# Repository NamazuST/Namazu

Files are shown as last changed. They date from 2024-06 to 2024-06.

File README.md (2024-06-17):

# Namazu: Low-cost tunable shaking table for vibration experiments under generic signals

This repository contains supplementary material to the publication ["2024 Grashorn, Bittner, Banse et al. - Namazu: Low-cost tunable shaking table for vibration experiments under generic signals"](https://doi.org/10.1007/s40799-024-00727-8) published in Experimental Techniques. The repository contains software, coded examples, firmware, and CAD files usable for vibrational experiments in the context of dynamic analysis of structures and stochastic dynamics in general.

Updates 17.06.2024

# Namazu architecture (Software & Hardware)

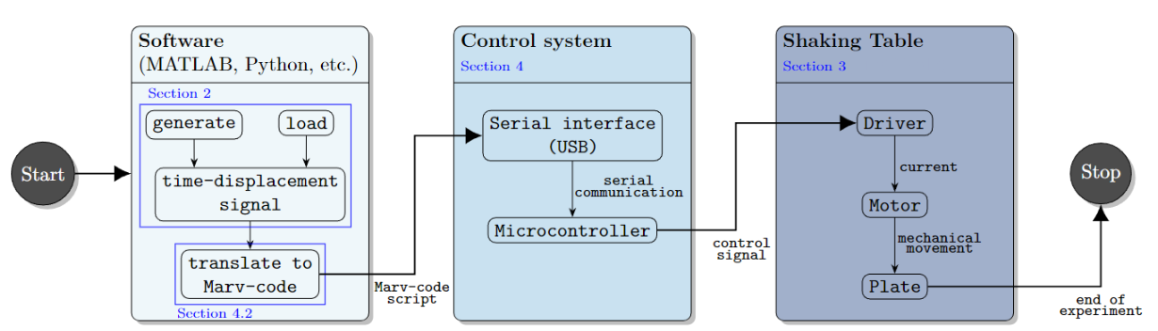
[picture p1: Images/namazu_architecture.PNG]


Figure 1: Flowchart and design concept of the Namazu framework, from signal generation via the software over the control system to plate motion, as in [our paper.](https://doi.org/10.1007/s40799-024-00727-8)

# Preparations

When this readme was written the following OS, platforms, and software were used:

- Windows 10.0.19041.4355 (professional)
- Microsoft Visual Studio Code 1.90.0 (VSC)
- MATLAB version 2023a
- Python version 3.12.3
- PlatformIO with Core 6.1.15 and Home 3.4.4

It is necessary to upload the firmware to a compatible ESP32 device. If this readme is not enough, you can find more information here: ["Namazu documentation"](https://namazu.de/). Please note that there are a multitude of ESP32 variants, so far we tested NodeMCU ESP32 WROOM32 and Firebeetle ESP32 modules. Please also note that we cannot test every variant and we are currently not recommending using ESP32-S2 or -C3 variants, since this could require code adaptations.

# Flashing of ESP32

Connect the ESP32 via a USB cable with your computer and identify the USB port by e.g. the device manager or PlatformIO.

In Windows you should located something like this:
"Port: COM3; Description: Silicon Labs CP210x USB to UART Bridge (COM3); Hardware: USB VID:PID=10C4:EA60 SER=0001 LOCATION=1-6"
The port ``` COM3 ``` could have a different number on your machine, depending on the USB socket you used.
In Linux the port is displayed differently (e.g. ```/dev/ttyUSB0```), but the description should remain the same.

Start VSC, locate and navigate to the Firmware folder (``\Firmware\``), start PlatformIO (in VSC), make sure the ESP32 has been located as described above.
To verify that everything is installed okay and no libraries are missing, press build. As indicated by <span style="color:orange"> *1.* </span> in Figure 2 below. Alternatively you can also use the buttons that are normally in the VSC UI located in the top-right corner, here see <span style="color:yellow"> *4.* </span> Figure 2.

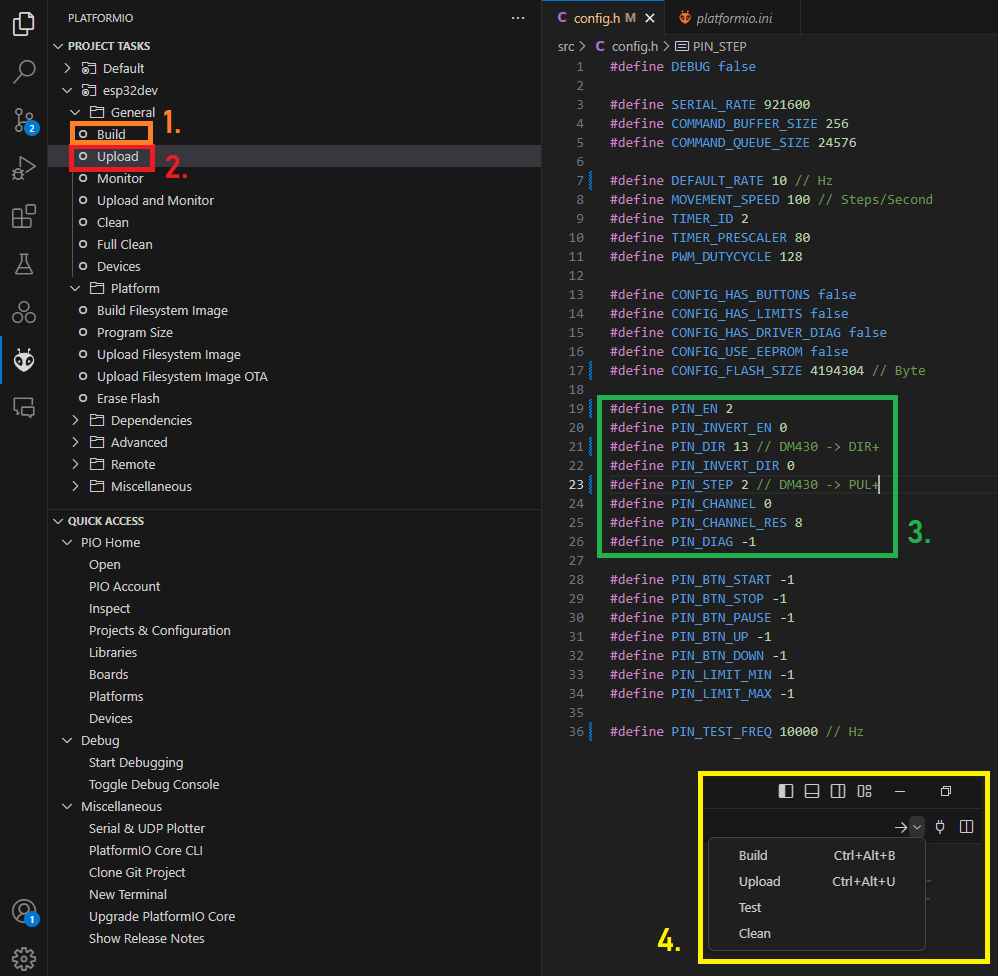
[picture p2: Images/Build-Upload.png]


Figure 2: PlatformIO.

A successful build should reveal this:



Figure 3: Build.

Then upload by pressing the upload button (inicated by <span style="color:red"> *2.* </span> in Figure 2 above) in PlatformIO. VSC will build again and then upload, the COM port should be identified automatically. 

A successful upload should display this:

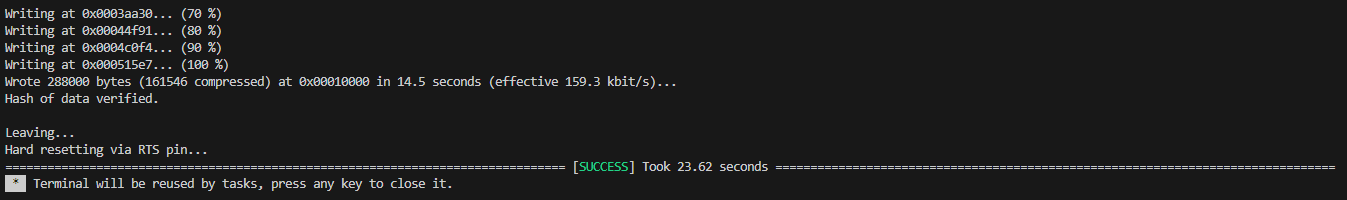
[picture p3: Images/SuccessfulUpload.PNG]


Figure 4: Upload.

The connecting pins of your ESP32 to the driver (in our case we used a DM430) are given in the window as in <span style="color:green"> *3.* </span> in Figure 2.

We advise you to not change or touch the firmware software in ``\Firmware\``, unless you know what you are doing.

## Safety Precautions

Remember, if you built Namazu, you are dealing with machinery.

<span style="color:red">*Disclaimer*</span>: The authors assume no responsibility or liability for any use of the software and provided ideas. By using this software, you acknowledge that you are solely responsible for any consequences that may arise. It is your responsibility to ensure you fully understand the operation and potential risks associated with the software and any machinery or systems it controls.

<span style="color:red">*Safety Warning*</span>: Always ensure you have a reliable power switch or safety mechanism to completely disconnect the machinery from the power grid in case of an emergency. Thoroughly assess the risks and plan your actions carefully. Double-check all connections and settings before proceeding. Safety should always be your top priority.

# Start with a main file

We provided coded examples and implementations for MATLAB and Python. Once you have your hardware ready and safety precautions were taken, we suggest to start with simple examples.

## MATLAB

For MATLAB, go to ```\MATLAB\MainCreateSimulation.m```. Here check line 179.

Make sure the correct com port is stated. If ran successfully a fixed harmonic with amplitude 1 and frequency 1 is started.

```Matlab
%% find shaking table controller on the correct COM port, COM port needs to be identified manually

dev = serialport("COM3",921600);
```

## Python

For Python, go to ```\Python\main_FixedHarmonic.py```. There check line 47.

Make sure the correct com port is stated. If ran successfully a fixed harmonic with amplitude 1 and frequency 1 is started.

```py
# Set the COM port and baud rate according to your ESP32 configuration
com_port = 'COM3'  # Change this to your COM port on Windows, e.g., 'COM3'
baud_rate = 921600  # Change this to match your ESP32 configuration

# Open the serial connection
ser = serial.Serial(com_port, baud_rate, timeout=1)
```

## Cite

For technical paper:

Grashorn J., Bittner, M., Banse, M. et al. (2024). Namazu: Low-cost tunable shaking table for vibration experiments under generic signals [https://doi.org/10.1007/s40799-024-00727-8](https://doi.org/10.1007/s40799-024-00727-8)

BibTex:
```
@article{NamazuEXTE2024,
    author = {Grashorn J., Bittner, M., Banse, M., Chang, X., Beer, M., Fau, A.},
    title = {Namazu: Low-cost tunable shaking table for vibration experiments under generic signals},
    year = {2024},
    publisher = {Springer Nature},
    journal = {Experimental Techniques},
    doi = {10.1007/s40799-024-00727-8},
}
```

For the repository:

https://github.com/NamazuST/Namazu

doi: https://zenodo.org/doi/10.5281/zenodo.10533795

BibTex:
```
@misc{NamazuRepo2024,
    author = {Grashorn J., Bittner, M., Banse, M.},
    title = {Namazu},
    year = {2024},
    publisher = {GitHub},
    journal = {GitHub repository},
    doi = {10.5281/zenodo.10533795},
}
```

## Showcase

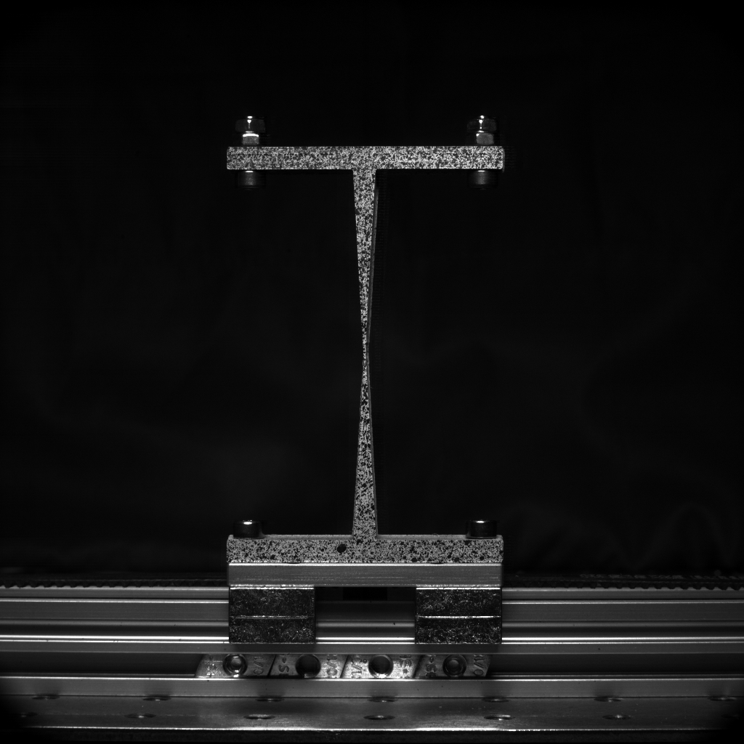
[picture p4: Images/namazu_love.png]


Figure 5: Experimental campaign with a Namazu realization, a 3D printed specimen and love

## Disclaimer
1. Content.
The author reserves the right not to be responsible for the topicality, correctness, completeness or quality of the information provided. Liability claims regarding damage caused by the use of any information provided, including any kind of information which is incomplete or incorrect, will therefore be rejected.
All offers are not-binding and without obligation. Parts of the pages or the complete publication including all offers and information might be extended, changed or partly or completely deleted by the author without separate announcement.
2. Responsibility. The authors assume no responsibility or liability for any use of the software and provided ideas. By using this software, you acknowledge that you are solely responsible for any consequences that may arise. It is your responsibility to ensure you fully understand the operation and potential risks associated with the software and any machinery or systems it controls.
3. Referrals and links.
The author is not responsible for any contents linked or referred to from his pages - unless he has full knowledge of illegal contents and would be able to prevent the visitors of his site fromviewing those pages. If any damage occurs by the use of information presented there, only the author of the respective pages might be liable, not the one who has linked to these pages. Furthermore the author is not liable for any postings or messages published by users of discussion boards, guestbooks or mailinglists provided on his page.
4. Copyright.
The author aims to use only non-copyrighted material or materials for which the author has obtained the necessary permissions. In cases where this is not possible, the copyright of the respective material will be indicated. The copyright for any original material created by the author is reserved. Duplication or use of such materials, including but not limited to images, diagrams, sounds, or texts, in other electronic or printed publications is permitted only under the terms of the included licenses:
    - Repository: Licensed under the Creative Commons Attribution-NonCommercial-ShareAlike 4.0 International (["CC BY-NC-SA 4.0"](https://creativecommons.org/licenses/by-nc-sa/4.0/)) license.
    - Technical Paper: Licensed under the Creative Commons Attribution 4.0 International (["CC BY 4.0"](https://creativecommons.org/licenses/by/4.0/)) license.
5. Privacy policy.
No privacy data is collected.
6. Legal validity of this disclaimer.
This disclaimer is to be regarded as part of the internet publication which you were referred from. If sections or individual terms of this statement are not legal or correct, the content or validity of the other parts remain uninfluenced by this fact.

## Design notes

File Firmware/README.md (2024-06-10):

# shakeIt

Available commands:

- **start** - Starts to move the motor to previously specified positions
- **stop** - immediately stops motor movement
- **info** - responds a line of information according the machines state:
`OK: Info: state: READY, mode POSITION, command 25 of 25, rate: 20hz, spmm: 10`

- **set rate nnn.nnn** - set the amout of positions to handle in one second
- **set spmm** - specifies how many steps the motor has to drive to move the carriage one millimeter
- **set mode position/velocity** - changes the interpretation of specified data
- **add nnn.nnn** - adds a position at the end of list
- **reset** - removes all positions from memory

This is an exemplary program to transmit via serial:
```
reset
set spmm 10
set rate 2.5
set mode pos
add 1
add 16
add 20
add 21
add 18
add 0.5
add -20
add -22
add -20
add -10
add 0
start
```

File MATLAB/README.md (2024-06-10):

# Shaking Table

## WARNING

!!!THE CONTROLLER SOFTWARE CURRENTLY HAS _NO_ SAFETY FEATURES (SUCH AS LIMIT SWITCHES), BE CAREFUL WHEN USING METHODS THAT WERE NOT TESTED EXTENSIVELY. INJURY TO YOU OR THE TABLE IS POSSIBLE!!!
It is entirely possible that settings in the simulation code and in the controller contradict each other. E.g. if the motor has a different value for the time step size, the table might behave very unexpectedly.

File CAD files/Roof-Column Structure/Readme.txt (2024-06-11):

Requirements: OpenSCAD

Scripts and OpenSCAD files to generate a 3D-printable roof-column structure for dynamical experiments. The structure is fully parameterized, where the spring stiffnesses can be changed based on thickness, number of windings etc. The roof can either be made with two or four springs.
A script (for Linux) is provided to export stl files for 3D-printing for the springs and the plate. An stl for the full assembly based on number of springs and number of storeys is also generated.
Attachement holes for MPU6050 sensors are included.

Usage:

- Change parameters to desired layout in scripts/Modules.scad, press F5 in OpenSCAD to view the model
- Run compile.sh from command line (Linux) to generate stl-files

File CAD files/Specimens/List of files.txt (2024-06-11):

- ContactColumn.stl
	Column with thin middle layer and contact area
	
- NotchedBeam.stl
	Beam with notch to induce damage

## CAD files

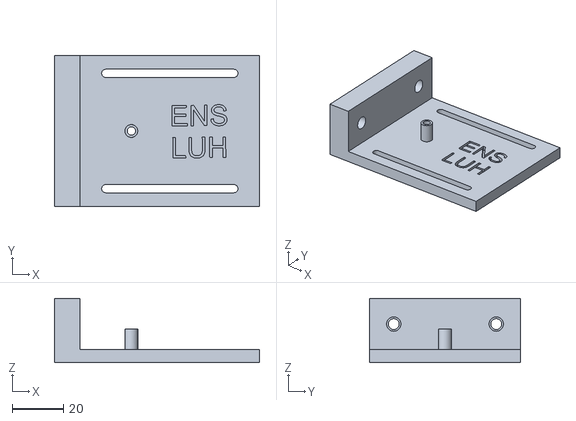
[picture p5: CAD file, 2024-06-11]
CAD files/Assembly/Belt tensioner/BeltTensioner_2.stl
80.0 x 58.8 x 25.0

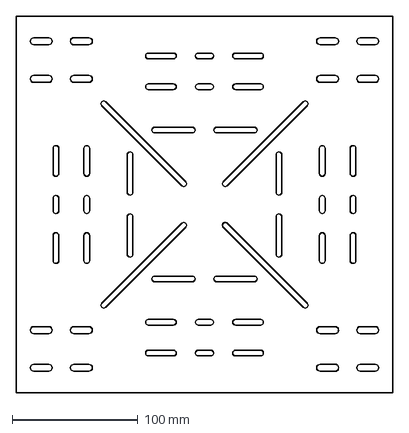
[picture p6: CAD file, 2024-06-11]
CAD files/Assembly/Plate/Plate.dxf
300.0 x 300.0 mm

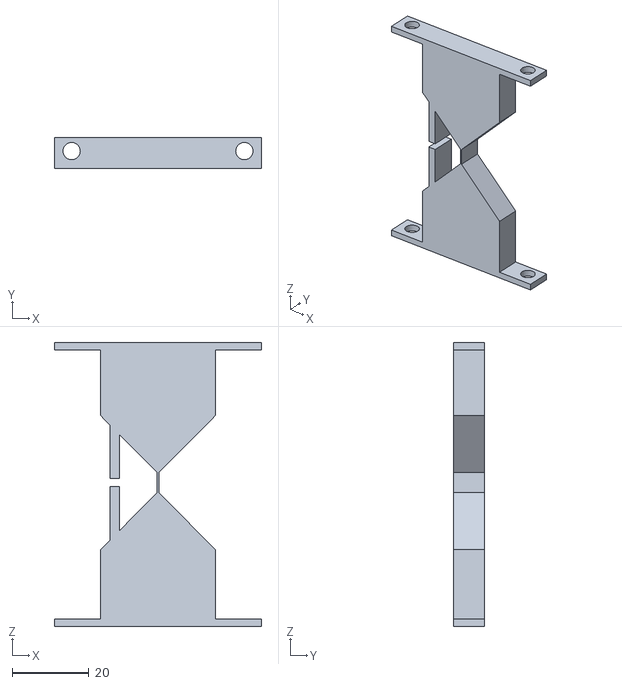
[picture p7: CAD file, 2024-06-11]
CAD files/Specimens/ContactColumn.stl
54.0 x 8.00 x 74.0

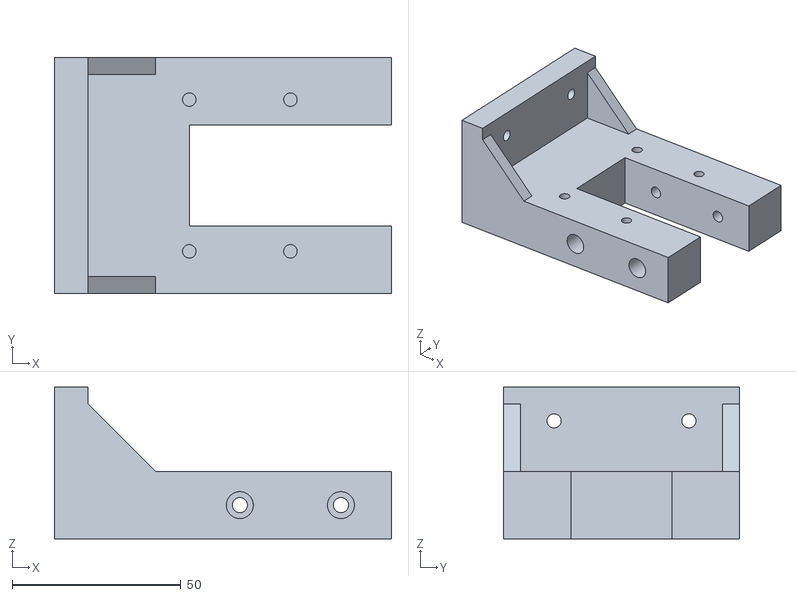
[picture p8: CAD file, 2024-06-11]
CAD files/Assembly/Belt tensioner/BeltTensioner_1.stl
100.0 x 70.0 x 45.0

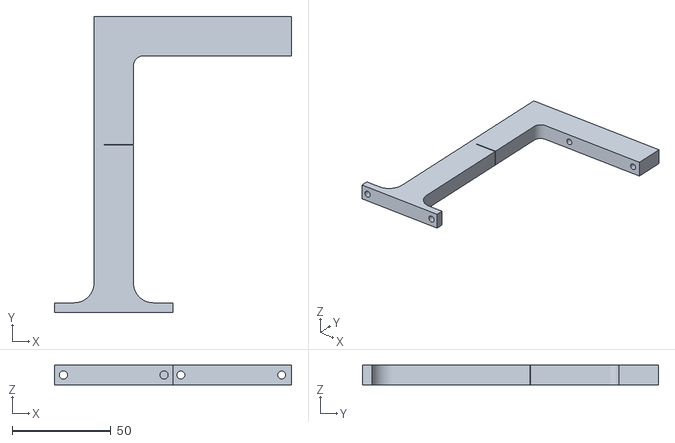
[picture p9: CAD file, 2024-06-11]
CAD files/Specimens/NotchedBeam.stl
120.0 x 150.0 x 10.0

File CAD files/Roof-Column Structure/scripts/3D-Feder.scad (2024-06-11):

include <Modules.scad>

Feder();

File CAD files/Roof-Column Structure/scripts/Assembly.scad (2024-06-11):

include <Modules.scad>

MPUattachments = 0;
dHole = 0;
nutS = 0;

module Assembly() {
        translate([0,0,wBase/2])
        for (i=[0:nStoreys-1]) {
            translate([0,0,i*storeyHeight])
            Storey();
        }
}

Assembly();

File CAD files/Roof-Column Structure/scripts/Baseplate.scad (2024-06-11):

include <Modules.scad>

Plate();

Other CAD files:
CAD files/Roof-Column Structure/scripts/BaseplateCutout.scad
CAD files/Roof-Column Structure/scripts/Modules.scad
CAD files/Roof-Column Structure/scripts/spring.scad

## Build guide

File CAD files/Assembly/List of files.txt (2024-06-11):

- Plate/Plate.dxf
	attachment plate to attach specimens on top of the table
	
- Belt tensioner/
	3D printable assembly to attach and tension the belt on the opposite side of the motor

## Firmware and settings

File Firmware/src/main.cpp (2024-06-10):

#include <Arduino.h>
#include "config.h"

#include <si_machine.hpp>
#include <si_interface.hpp>
#include <si_storage.hpp>

si::Storage storage;
si::Machine machine = si::Machine(storage);
si::Interface interface = si::Interface(machine);

#if CONFIG_HAS_BUTTONS
/* START - Button */
IRAM_ATTR void btn_start();
void start(void *) {
    interface.cmd_start();
    attachInterrupt(PIN_BTN_START,btn_start,FALLING);
}
IRAM_ATTR void btn_start() {
    detachInterrupt(PIN_BTN_START);
    xTaskCreate(
        start,              /* Task function. */
        "BtnStart",         /* String with name of task. */
        4096,               /* Stack size in bytes. */
        NULL,               /* Parameter passed as input of the task */
        0,                  /* Priority of the task. */
        NULL
    );
}

/* STOP - Button */
IRAM_ATTR void btn_stop();
void stop(void *) {
    interface.cmd_stop();
    attachInterrupt(PIN_BTN_STOP,btn_stop,FALLING);
}
IRAM_ATTR void btn_stop() {
    detachInterrupt(PIN_BTN_STOP);
    xTaskCreate(
        stop,               /* Task function. */
        "BtnStop",          /* String with name of task. */
        4096,               /* Stack size in bytes. */
        NULL,               /* Parameter passed as input of the task */
        0,                  /* Priority of the task. */
        NULL
    );
}

/* PAUSE - Button */
IRAM_ATTR void btn_pause();
void pause(void *) {
    machine.pause();
    attachInterrupt(PIN_BTN_PAUSE,btn_pause,FALLING);
}
IRAM_ATTR void btn_pause() {
    detachInterrupt(PIN_BTN_PAUSE);
    xTaskCreate(
        pause,              /* Task function. */
        "BtnPause",         /* String with name of task. */
        4096,               /* Stack size in bytes. */
        NULL,               /* Parameter passed as input of the task */
        0,                  /* Priority of the task. */
        NULL
    );
}

/* UP - Button */
IRAM_ATTR void btn_up_rise();
void up_rise(void *) {
    machine.stop();
    attachInterrupt(PIN_BTN_UP,btn_up_rise,FALLING);
}
IRAM_ATTR void btn_up_rise() {
    detachInterrupt(PIN_BTN_UP);
    xTaskCreate(
        up_rise,            /* Task function. */
        "BtnUpRise",        /* String with name of task. */
        4096,               /* Stack size in bytes. */
        NULL,               /* Parameter passed as input of the task */
        0,                  /* Priority of the task. */
        NULL
    );
}
IRAM_ATTR void btn_up_fall();
void up_fall(void *) {
    machine.move_up();
    attachInterrupt(PIN_BTN_UP,btn_up_rise,RISING);
}
IRAM_ATTR void btn_up_fall() {
    detachInterrupt(PIN_BTN_UP);
    xTaskCreate(
        up_fall,            /* Task function. */
        "BtnUpFall",        /* String with name of task. */
        4096,               /* Stack size in bytes. */
        NULL,               /* Parameter passed as input of the task */
        0,                  /* Priority of the task. */
        NULL
    );
}

/* DOWN - Button */
IRAM_ATTR void btn_down_rise();
void down_rise(void *) {
    machine.stop();
    attachInterrupt(PIN_BTN_DOWN,btn_down_rise,FALLING);
}
IRAM_ATTR void btn_down_rise() {
    detachInterrupt(PIN_BTN_DOWN);
    xTaskCreate(
        down_rise,          /* Task function. */
        "BtnUpRise",        /* String with name of task. */
        4096,               /* Stack size in bytes. */
        NULL,               /* Parameter passed as input of the task */
        0,                  /* Priority of the task. */
        NULL
    );
}
IRAM_ATTR void btn_down_fall();
void down_fall(void *) {
    machine.move_down();
    attachInterrupt(PIN_BTN_DOWN,btn_down_rise,RISING);
}
IRAM_ATTR void btn_down_fall() {
    detachInterrupt(PIN_BTN_DOWN);
    xTaskCreate(
        down_fall,            /* Task function. */
        "BtnUpFall",        /* String with name of task. */
        4096,               /* Stack size in bytes. */
        NULL,               /* Parameter passed as input of the task */
        0,                  /* Priority of the task. */
        NULL
    );
}
#endif

#if CONFIG_HAS_LIMITS
/* Limit Switch MIN */
IRAM_ATTR void limit_min();
void min(void *) {
    machine.limit_min();
    attachInterrupt(PIN_LIMIT_MIN,limit_min,FALLING);
}
IRAM_ATTR void limit_min() {
    detachInterrupt(PIN_LIMIT_MIN);
    xTaskCreate(
        min,              /* Task function. */
        "LimitMin",         /* String with name of task. */
        4096,               /* Stack size in bytes. */
        NULL,               /* Parameter passed as input of the task */
        0,                  /* Priority of the task. */
        NULL
    );
}

/* Limit Switch MAX */
IRAM_ATTR void limit_max();
void max(void *) {
    machine.limit_max();
    attachInterrupt(PIN_LIMIT_MAX,limit_max,FALLING);
}
IRAM_ATTR void limit_max() {
    detachInterrupt(PIN_LIMIT_MAX);
    xTaskCreate(
        max,                /* Task function. */
        "LimitMax",         /* String with name of task. */
        4096,               /* Stack size in bytes. */
        NULL,               /* Parameter passed as input of the task */
        0,                  /* Priority of the task. */
        NULL
    );
}
#endif

/* MAIN */
void setup() {
    interface.init();
    machine.init();
    if (!storage.init()) {
        Serial.println("FAILED TO INITALIZE STORAGE");
    }
#if CONFIG_HAS_LIMITS
    attachInterrupt(PIN_LIMIT_MIN,limit_min,FALLING);
    attachInterrupt(PIN_LIMIT_MAX,limit_max,FALLING);
#endif
#if CONFIG_HAS_BUTTONS
    attachInterrupt(PIN_BTN_START,btn_start,FALLING);
    attachInterrupt(PIN_BTN_STOP,btn_stop,FALLING);
    attachInterrupt(PIN_BTN_PAUSE,btn_pause,FALLING);
    attachInterrupt(PIN_BTN_UP,btn_up_fall,FALLING);
    attachInterrupt(PIN_BTN_DOWN,btn_down_fall,FALLING);
#endif

}

void loop() {
    interface.loop();
}

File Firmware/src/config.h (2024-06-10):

#define DEBUG false

#define SERIAL_RATE 921600
#define COMMAND_BUFFER_SIZE 256
#define COMMAND_QUEUE_SIZE 24576

#define DEFAULT_RATE 10 // Hz
#define MOVEMENT_SPEED 100 // Steps/Second
#define TIMER_ID 2
#define TIMER_PRESCALER 80
#define PWM_DUTYCYCLE 128

#define CONFIG_HAS_BUTTONS false
#define CONFIG_HAS_LIMITS false
#define CONFIG_HAS_DRIVER_DIAG false
#define CONFIG_USE_EEPROM false
#define CONFIG_FLASH_SIZE 4194304 // Byte

#define PIN_EN 2 
#define PIN_INVERT_EN 0
#define PIN_DIR 13 // DM430 -> DIR+
#define PIN_INVERT_DIR 0
#define PIN_STEP 2 // DM430 -> PUL+
#define PIN_CHANNEL 0
#define PIN_CHANNEL_RES 8
#define PIN_DIAG -1

#define PIN_BTN_START -1
#define PIN_BTN_STOP -1
#define PIN_BTN_PAUSE -1
#define PIN_BTN_UP -1
#define PIN_BTN_DOWN -1
#define PIN_LIMIT_MIN -1
#define PIN_LIMIT_MAX -1

#define PIN_TEST_FREQ 10000 // Hz

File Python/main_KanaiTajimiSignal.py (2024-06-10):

###################################################################################################################################
#Main script to simulate and send a stochastic signal based on the Kanai-Tajimi Spectrum to the ESP32 -> Driver -> Motor
#Import shaking data object
from Classes import ShakingDataClass
#Import Namazu framework functions
from Methods import InputSignalMethods
from Functions import WriteMarvCode
from Functions import SendCode2Motor
#Import utilities
import matplotlib.pyplot as plt
import numpy as np

# Create an instance of the ShakingData class
shaking_data_instance = ShakingDataClass.ShakingData()

#Simulation parameters
stepsPerSecond = 100    #Steps performed per second
shaking_data_instance.motorRate = stepsPerSecond
maxT = 5               #Maximum number of time for the simulation in seconds
maxF = 12              #Maximum frequency
nOmega = 50            #Number of discretized frequencies
# Kanai-Tajimi scale parameters
w_g = 9 * 2 * np.pi  # Peak frequency
beta_g = 0.6
# Scale whole PSD function amplitude
S_0 = 0.01

# Define the PSD function
def PSD_KT(omega):
    numerator = (w_g ** 4 + (2 * beta_g * w_g * omega) ** 2)
    denominator = ((w_g ** 2 - omega ** 2) ** 2 + (2 * beta_g * w_g * omega) ** 2)
    return numerator / denominator * S_0

# Store the PSD function for later access
shaking_data_instance.psdFunc = PSD_KT

# Define output file name
shaking_data_instance.fileName = f"Shinozuka_Kanai-Tajimi_{maxF}_{nOmega}_{maxT}_{stepsPerSecond}"

#Simulate a fixed or mixed harmonic signal
[pos_out, t_out, dt_out, shaking_data_instance] = InputSignalMethods.SimulateShinozuka(shaking_data_instance, maxT, maxF*2*np.pi, nOmega)

# Create a line plot for one frequency
plt.plot(t_out, pos_out)
# displaying the title
plt.title(shaking_data_instance.fileName)
plt.xlabel("time in [s]")
plt.ylabel("x in [mm]")

# Show the plot
plt.show()

#Store the input signal in the shaking data object
shaking_data_instance.inputSignal= [t_out, pos_out]

#Write the marvCode
shaking_data_instance = WriteMarvCode.WriteMarvCode(shaking_data_instance)

#This needs to be send to the ESP32
import serial # pyserial is required
import time

# Set the COM port and baud rate according to your ESP32 configuration
com_port = 'COM3'  # Change this to your COM port on Windows, e.g., 'COM3'
baud_rate = 921600  # Change this to match your ESP32 configuration

# Open the serial connection
ser = serial.Serial(com_port, baud_rate, timeout=1)
# Flush any existing data in the input buffer
ser.flushInput()

# Send the marvCode (displacement history) to ESP32
SendCode2Motor.SendMarvCode2Motor(ser, shaking_data_instance)

prompt_response = input("To continue, press 'y': ")
if prompt_response.lower() == 'y':
    print("Continuing...")
    # Start the motor
    SendCode2Motor.SendCmd2Motor(ser, 'start')
    time.sleep(t_out[-1]+5)  # Wait for T+5 seconds
else:
    print("Not continuing.")

# Close port
print("Shaking finished. Closing port...")
ser.close()
print("Port closed.")

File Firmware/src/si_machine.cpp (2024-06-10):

#include <si_machine.hpp>
#include <Arduino.h>
#include <config.h>
#include <nvs_flash.h>

si::Machine* si::Machine::_instance;

si::Machine::Machine(Storage& storage)
 : _storage(storage) {
    _instance = this;
}

void si::Machine::init() {

    _config = _storage.load_config();
    if (_config.timer_interval == 0) {
        _config.timer_interval = (1000000UL / DEFAULT_RATE);
    }
    if (_config.rate.divisor == 0) {
        _config.rate = {DEFAULT_RATE,1};
    }
    if (_config.spmm.divisor == 0) {
        _config.spmm = {0,1};
    }
    if (_config.mode == UNSET) {
        _config.mode = POSITION;
    }

    _status.cmd_cnt = _storage.load_commands(_cur_cmd_queue, 0);
    if (_status.cmd_cnt > (COMMAND_QUEUE_SIZE / 2)) {
        _storage.load_commands(_spare_cmd_queue, (COMMAND_QUEUE_SIZE / 2));
    }
    if (_status.cmd_cnt > 0) {
        _state = READY;
    }

    _queue = xQueueCreate( 10, sizeof( int ) );
    _queue_flip = xQueueCreate( 2, sizeof( int* ) );

    _cmd_timer = timerBegin(TIMER_ID, TIMER_PRESCALER, true);
    timerAlarmWrite(_cmd_timer, _config.timer_interval, true);
    timerAttachInterrupt(_cmd_timer, call_next_cmd, true);

    xTaskCreate(
        call_set_frequence, /* Task function. */
        "SetFrequence",     /* String with name of task. */
        4096,               /* Stack size in bytes. */
        NULL,               /* Parameter passed as input of the task */
        0,                  /* Priority of the task. */
        NULL
    );
    xTaskCreate(
        call_fill_queue,    /* Task function. */
        "FillQueue",        /* String with name of task. */
        4096,               /* Stack size in bytes. */
        NULL,               /* Parameter passed as input of the task */
        1,                  /* Priority of the task. */
        NULL
    );
    
}

void si::Machine::start() {
    switch (_state){
    case READY:
        _status.cmd_idx = 0;
        _status.pos = 0;
        if (_new_cmd) {
            _storage.write_commands(_cmd_queue_0, 0, _status.cmd_cnt);
            if (_status.cmd_cnt > (COMMAND_QUEUE_SIZE / 2)) {
                _storage.write_commands(_cmd_queue_1, (COMMAND_QUEUE_SIZE / 2), _status.cmd_cnt);
            }
            if (_cmd_queue_buf != nullptr) {
                _storage.write_commands(_cmd_queue_1, (_cmd_segment * (COMMAND_QUEUE_SIZE / 2)), _status.cmd_cnt);
            }
            _new_cmd = false;
        }
    case PAUSED:
        _state = RUNNING;
        timerAlarmEnable(_cmd_timer);
        timerStart(_cmd_timer);
        digitalWrite(PIN_EN, HIGH != PIN_INVERT_EN);
    default:
        return;
    }
}

void si::Machine::stop() {
    timerAlarmDisable(_cmd_timer);
    if (_state == RUNNING) {
        size_t cmd_idx = 0;
        _state = READY;
        xQueueSend(_queue, &cmd_idx, portMAX_DELAY);
    }
}

void si::Machine::pause() {
    if (_state == RUNNING) {
        size_t cmd_idx = 0;
        _state = PAUSED;
        xQueueSend(_queue, &cmd_idx, portMAX_DELAY);
    }
}

bool si::Machine::is_running() {
    return (_state == RUNNING);
}

bool si::Machine::set_rate(unsigned_frac_t rate) {
    if (_state == IDLE || _state == READY) {
        uint64_t factor = 1000000UL * (uint64_t)rate.divisor;
        _config.timer_interval = factor / (uint64_t)rate.factor;
        _config.rate = rate;
        timerAlarmWrite(_cmd_timer, _config.timer_interval, true);
        _storage.write_config(&_config);
        return true;
    }
    return false;
}

bool si::Machine::set_spmm(unsigned_frac_t spmm) {
    _config.spmm = spmm;
    _storage.write_config(&_config);
    return true;
}

si::Machine::state_t si::Machine::get_state() {
    return _state;
}

si::mode_t si::Machine::get_mode() {
    return _config.mode;
}

uint64_t si::Machine::get_timer_interval() {
    return _config.timer_interval;
}

si::Machine::fault_t si::Machine::get_fault() {
    return _fault;
}

si::config_t si::Machine::get_config() {
    return _config;
}

si::Machine::status_t si::Machine::get_status() {
    return _status;
}

bool si::Machine::add_position(frac_t pos) {
    if (_state == IDLE) {
        _state = READY;
    }
    if (_status.cmd_cnt < (COMMAND_QUEUE_SIZE / 2)) {
        _cmd_queue_0[_status.cmd_cnt++] = mulFrac2Int(pos, _config.spmm);
#if DEBUG
        Serial.println("stored into cur_q");
#endif
    } else if (_status.cmd_cnt < COMMAND_QUEUE_SIZE) {
        _cmd_queue_1[(_status.cmd_cnt++) - (COMMAND_QUEUE_SIZE / 2)] = mulFrac2Int(pos, _config.spmm);
#if DEBUG
        Serial.println("stored into spare_q");
#endif
    } else {
        size_t segment = _status.cmd_cnt / (COMMAND_QUEUE_SIZE / 2);
        if (segment != _cmd_segment) {
#if DEBUG
            Serial.println("new Segment");
#endif
            if (_cmd_queue_buf != nullptr) {
#if DEBUG
                Serial.println("Found spareQ, write and free mem");
#endif
                _storage.write_commands(_cmd_queue_buf, (_cmd_segment * (COMMAND_QUEUE_SIZE / 2)), (_status.cmd_cnt + 1));
                free(_cmd_queue_buf);
            }
            _cmd_queue_buf = (int*) malloc((COMMAND_QUEUE_SIZE / 2) * sizeof(int));
            if (_cmd_queue_buf == nullptr) {
                Serial.println("ERR: failed to allocate memory for commands");
                return false;
            }
#if DEBUG
            Serial.println("got dyn mem");
#endif
            _cmd_queue_buf[(_status.cmd_cnt++) - (segment * (COMMAND_QUEUE_SIZE / 2))] = mulFrac2Int(pos, _config.spmm);
            _cmd_segment = segment;
        } else {
#if DEBUG
            Serial.println("stored into dyn mem");
#endif
            _cmd_queue_buf[(_status.cmd_cnt++) - (segment * (COMMAND_QUEUE_SIZE / 2))] = mulFrac2Int(pos, _config.spmm);
        }
    }
    _new_cmd = true;
    return true;
}

bool si::Machine::reset() {
#if CONFIG_USE_EEPROM
    nvs_flash_erase(); // erase the NVS partition and...
    nvs_flash_init();
    _storage.write_config(&_config);
#endif
    if (_state == READY) {
        _status.cmd_cnt = 0;
        _status.cmd_idx = 0;
        _status.pos = 0;
        _state = IDLE;
        return true;
    }
    return false;
}

bool si::Machine::move_up() {
    if (_state == RUNNING || _state == FAULT) return false;
    _state = MANUAL;
    _frequency = (double)(MOVEMENT_SPEED) * (1000000.0 / (double)_config.timer_interval);
    ledcWriteTone(PIN_CHANNEL, _frequency);
    digitalWrite(PIN_DIR, HIGH != PIN_INVERT_DIR);
    return true;
}

bool si::Machine::move_down() {
    if (_state == RUNNING || _state == FAULT) return false;
    _state = MANUAL;
    _frequency = (double)(MOVEMENT_SPEED) * (1000000.0 / (double)_config.timer_interval);
    ledcWriteTone(PIN_CHANNEL, _frequency);
    digitalWrite(PIN_DIR, LOW != PIN_INVERT_DIR);
    return true;
}
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

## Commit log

2024-06-11 Added CAD files for table and specimens
    [3D-Feder.scad, Assembly.scad, Baseplate.scad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]
2024-06-11 added readme to CAD files
2024-06-17 Release 1.1
    Fix image path, github is case-sensitive
2026-02-24 Add comment for arduino specific settings.
2026-03-23 Add first sensor rig configuration.
